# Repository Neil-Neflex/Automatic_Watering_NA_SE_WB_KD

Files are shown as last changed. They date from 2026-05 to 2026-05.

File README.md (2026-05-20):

Ce dépôt est organisé de manière à séparer la documentation de conception du code source technique. Pour naviguer efficacement, le projet utilise deux branches distinctes.

## Organisation des branches

- **Branche main**: Centralise la documentation, les rapports de projet et les études d'impact.
- **Branche partie-logicielle**: Contient exclusivement le code source et les fichiers de configuration.

## Contenu de la branche Main

- **DOCS**: Ressources techniques et rapports des membres du groupe par séance.
- **ecoconception**: Analyse du cycle de vie et choix techniques pour minimiser l'empreinte énergétique.
- **Hardware-pcb-eagle**: Schémas électroniques et fichiers PCB réalisés sous Eagle.
- **ProjetS7.pdf**: Présentation S8.
- **RAPPORT.pdf**: Rapport de synthèse présentant les objectifs et résultats du semestre 7 et 8.

## Architecture logicielle

Le code est segmenté par modules fonctionnels(exemple) :
- **Watering_System.ino**: Point d'entrée principal du programme.
- **SensorManagment (.cpp/.h)**: Logique de traitement des capteurs.
- **VanneCase (.h)**: Gestion des états de l'électrovanne.
- **ModuleHorloge (.cpp/.h)**: Gestion du temps réel (RTC).

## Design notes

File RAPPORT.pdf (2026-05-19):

## Conception d'une station d'arrosage autonome sous ESP32

Projet réalisé dans le cadre de la formation en Ingénierie des Systèmes Embarqués en 4e année
ELSE 4 FISA

### Présenté par :

Ndeye Khady DIOP

Salma ELFIACHE

Wissal BELLAHCEN

### Sous la direction de :

M. Christian PETER

## 1. Introduction générale

## 1.1 Contexte du projet

Dans un contexte mondial marqué par le dérèglement climatique, la gestion raisonnée de l’irrigation représente un enjeu croissant. L’arrosage manuel présente des limites importantes: ils ne tiennent pas compte des conditions météorologiques réelles et conduisent fréquemment à une sur-irrigation néfaste pour l’environnement.
Ce projet s’inscrit dans le cadre du module d'électronique, visant à concevoir un système d’arrosage automatique intelligent, capable de piloter jusqu'à quatres zones d’irrigation de façon indépendante, tout en s’adaptant aux conditions extérieures mesurées en temps réel (température, humidité de l'air, humidité du sol, pluviométrie) .

## 1.2 Problématique

Comment concevoir un système d’arrosage capable de :

- Commander jusqu’à 4 électrovannes de façon indépendante,
- S’adapter en temps réel aux conditions météorologiques (pluie, température, humidité),
- Fonctionner sur batterie avec une autonomie maximale,
- Afficher clairement les informations à l’utilisateur

## 1.3 Objectifs et fonctionnalités attendues

- Pilotage de 4 vannes motorisées 12V (commande impulsionnelle).
- Planification horaire : heure de début et fréquence (en heures) réglables.
- Adaptation automatique : modulation de la durée d’arrosage selon la température et l’humidité de l’air ; annulation en cas de pluie ou de risque de gel.
- Mesure et affichage : température, humidité relative de l'air, humidité du sol (sonde analogique), cumul pluviométrique quotidien, état des vannes.

- Interface utilisateur : écran TFT couleur (ILI9341), avec affichage de logos et de textes.
- Alimentation sur batterie (3,7V Li‑ion) avec convertisseur élévateur 12V pour les vannes.
- Économie d’énergie : utilisation du mode deep sleep et du coprocesseur ULP pour le comptage de la pluie.

## 1.4 Cahier des charges (exigences et contraintes)

## 1.4.1 Description générale

Le système gère 4 circuits d’irrigation indépendants via 4 électrovannes. Les vannes peuvent être activées ou désactivées ; elles sont déclenchées successivement pour éviter une chute de débit. La durée d’arrosage est individuelle par zone, la fréquence est commune. Les mesures des capteurs, la date et l’heure sont affichées en temps réel.

### 1.4.2 Contraintes générales

Domaine | Exigence
Alimentation | Batterie 3,7V + convertisseur 12V pour vannes.
Étanchéité | Boîtier IP65 (extérieur).
Coût | Total <150 € (composants + PCB).
Autonomie | Deep sleep majoritaire, consommation <10 µA en veille.
Reproductibilité | Schéma Eagle, code commenté, BOM fournie.

Simplicité | Pas de dépendance à un serveur distant, paramètres modifiables dans le code.
Interfaces | Compatibilité avec l’ESP32

### 1.4.3 Spécifications fonctionnelles

- Vannes : commande impulsionnelle (5s) non‑bloquante ; pas d’ouverture simultanée.
- Planification : heures de début fixes (ex. 20h00, 20h30…), fréquence en heures (calcul par modulo jours), durée individuelle (minutes).
- Capteurs : DHT22 (température, humidité), pluviomètre à auget (0,2794 mm/basculement), sonde d’humidité du sol (analogique, 0–100%).
- RTC : DS3231 (I2C, pile CR2032 de secours).
- Affichage : écran TFT ILI9341 (SPI), rafraîchissement par flags, logos PNG.
- Adaptation : annulation si pluie >5 mm, T°<4°C, ou sol ≥60% ; modulation durée : +30% si T°≥30°C, –20% si humidité air ≥80%, +20% si sol ≤20%.
- Deep sleep : entrée après 120 secondes d’inactivité (pas d’impulsion pluie, pas d’arrosage). Réveil toutes les 5 minutes. ULP actif pour compter la pluie.

(Les spécifications techniques détaillées des composants sont reportées dans l’état de l’art, section 2.)

## 2. État de l’art et choix technologiques

## 2.1 Choix de l’unité de traitement – ESP32-WROOM-32D

L’ESP32 a été sélectionné pour ses caractéristiques :

- Double cœur Xtensa LX6 à 240 MHz, puissance suffisante pour l’affichage et les algorithmes.
- Coprocesseur ULP (Ultra Low Power) exécutant un programme en assembleur même en deep sleep – indispensable pour compter les impulsions du pluviomètre sans réveiller le CPU.
- Consommation : <10 µA en deep sleep (ULP actif).
- Interfaces : SPI (écran), I2C (RTC), ADC (sol), GPIO (vannes).
- Wi‑Fi/Bluetooth intégrés pour évolutions futures.

Caractéristiques principales : SRAM 520 Ko, Flash 4 Mo, 38 GPIO, ADC 12 bits, alimentation 3,0–3,6 V.

## 2.2 Sélection des capteurs et actionneurs

Type | Modèle | Précision / Sensibilité

Interface

Température /
humidité
DHT22 | ±0,5°C, ±2% HR | 1‑wire (GPIO14,
pull‑up 4,7kΩ)
Pluviomètre | Lexca001 | 0,2794
mm/basculeme
nt

Contact sec,
GPIO34 (pull‑up
externe 10kΩ)

Humidité du
sol

Sonde
capacitive

0–100%
(calibration)

Analogique,
GPIO35

Électrovanne ACARPS IP65
(3 fils)

12V DC, 6W,
commande
impulsionnelle
5s

2 GPIO par
vanne
(ouverture/ferm
eture) via
MOSFET

Détail des vannes : type latching (maintien de position sans courant après impulsion). Pilotage par N‑MOS BSS123 (côté ESP32) et P‑MOS DMP3098 (côté 12V). Résistances de 330 Ω sur les grilles.

## 2.3 Gestion de l’énergie

L’autonomie sur batterie repose sur trois axes complémentaires :

- Architecture d’alimentation : batterie Li-ion 18650 (3,7V, 3000 mAh). Alimentation directe de l’ESP32 (régulateur interne). Un convertisseur élévateur MT3608 fournit le 12V aux vannes. Une diode Schottky SS34 protège contre les inversions de polarité.
- Vannes latching : consommation uniquement pendant l’impulsion de 5 secondes (≈30 J par action), puis zéro.
- Mode deep sleep de l’ESP32 : le CPU est éteint la plupart du temps, seule l’ULP tourne. Consommation <10 µA. L’entrée en veille est conditionnée par l’absence d’arrosage et un délai d’inactivité de 120 secondes. Réveil périodique toutes les 5 minutes.

## 2.4 Interface homme‑machine – Écran TFT ILI9341

Écran 2,4 pouces, 240×320 pixels, 16 bits, piloté en SPI.
Brochage utilisé : MOSI=23, MISO=19, SCK=18, CS=15, DC=5, RST=4, LED=13. Logos PNG (température, humidité, pluie, terre) stockés en mémoire Flash (fichier images.h) et décodés par la bibliothèque PNGdec.

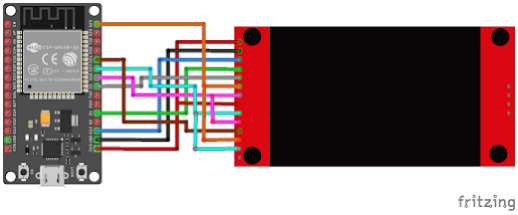
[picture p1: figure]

Shémat de cablage provenant du site : https://electroniqueamateur.blogspot.com/2021/05/utilisation-dun-ecran-ta ctile-tft-spi.html

Voici le branchement de l'écran sur le module ESP32:

- Broche VCC de l'écran: sortie 3,3 V de l'ESP32
- Broche GND de l'écran: broche GND de l'ESP32
- Broche CS de l'écran: broche D15 de l'ESP32
- Broche Reset de l'écran: broche D4 de l'ESP32
- Broche DC de l'écran: broche D5 de l'ESP32
- Broche SDI (MOSI) de l'écran: broche D23 de l'ESP32
- Broche SCK de l'écran: broche D18 de l'ESP32
- Broche LED de l'écran: sortie 3,3 V de l'ESP32
- Broche CDCK (MISO) de l'écran: broche D19 de l'ESP32
- Broche T_CLK de l'écran: broche D18 de l'ESP32
- Broche T_CS de l'écran: broche D21 de l'ESP32
- Broche T_DIN de l'écran: broche D23 de l'ESP32
- Broche T_DO de l'écran: broche D19 de l'ESP32
- Broche T_IRQ de l'écran: pas branchée

## 3. Architecture globale du système

## 3.1 Synoptique matériel

Le système repose sur un ESP32-WROOM assurant l’acquisition des données environnementales, leur traitement et la commande des électrovannes. L’alimentation des actionneurs est assurée par une conversion DC-DC élévatrice, tandis que l’interface utilisateur est réalisée via un écran TFT SPI

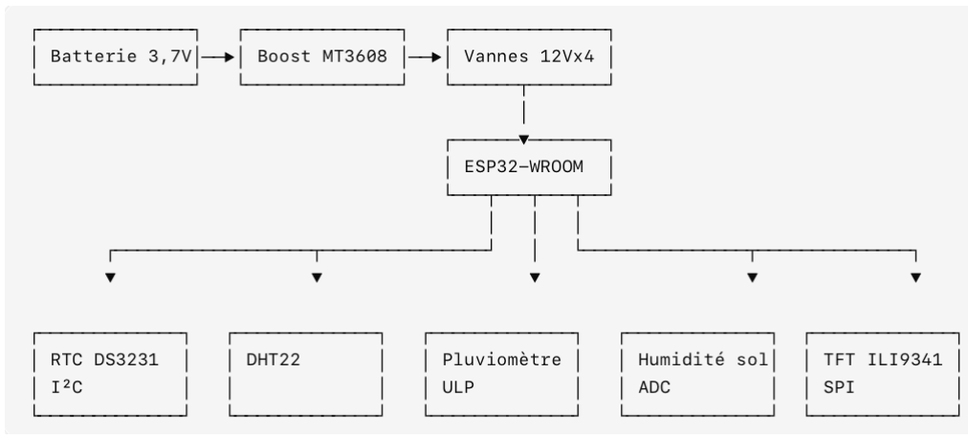
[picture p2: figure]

## 3.2 Modes de fonctionnement

Le système opère selon deux modes distincts, gérés dynamiquement en fonction de l'activité détectée.

Mode actif. À chaque démarrage ou réveil, l'ESP32 initialise l'ensemble des périphériques (RTC DS3231, écran TFT, capteur DHT22) et lance la boucle principale. Celle-ci exécute quatre tâches non-bloquantes par des timers millis() : la mise à jour de l'affichage à la seconde, la lecture des capteurs toutes les 5 secondes, la lecture du compteur pluviométrique toutes les 2 secondes, et la vérification du planning d'arrosage à chaque seconde. L'affichage est actif et l'interface utilisateur réactive aux appuis sur les boutons.

Mode veille profonde (Deep Sleep). Lorsque les conditions du garde-fou sont réunies, l'ESP32 sauvegarde les données persistantes (cumul de pluie, timestamps de fin d'arrosage, horodatage de la dernière pluie) dans la mémoire RTC — la seule zone mémoire qui survit au Deep Sleep — puis entre en sommeil. Un réveil périodique par timer permet de vérifier régulièrement si un arrosage planifié doit être déclenché. Lors du réveil, le système distingue un premier démarrage (remise à zéro de tous les compteurs et initialisation de l'ULP) d'un réveil depuis la veille (restauration des valeurs mémorisées), avant de reprendre la boucle principale.

## 4. Conception logicielle

## 4.1 Architecture Orientée Objet (POO)

Le code est découpé en plusieurs classes pour faciliter la maintenance et l’évolution :

- Case (classe abstraite) : représente une zone rectangulaire de l’écran, avec position, taille, couleur de fond, et un flag de modification.
- SensorCase : hérite de Case, ajoute une valeur entière, une unité, un logo PNG, et la méthode draw() pour afficher ces informations.
- VanneCase : hérite de Case, ajoute un nom, une fréquence (heures), une durée (minutes), l’état (ouverte/fermée) et les GPIO de commande.
- Interface: gère l’écran global, l’affichage de l’heure, et appelle le dessin des cases.
- SensorManagment : regroupe la lecture des capteurs (DHT22, RTC, ULP, sol) et met à jour les objets SensorCase correspondants.

Cette modularité permet d’ajouter facilement un nouveau capteur ou une nouvelle vanne.

## 4.2 Optimisation de l'Interface Homme-Machine

Affichage par flags : chaque case possède un booléen flag qui passe à 1 quand sa valeur ou sa couleur change. La fonction Update() ne redessine que les cases dont le flag est à 1, puis le remet à 0. Cela évite de rafraîchir tout l’écran à chaque seconde et réduit la charge CPU.
Logos PNG : les icônes (température, humidité, pluie, terre) sont stockées en mémoire Flash (via images.h) et décodées avec la bibliothèque PNGdec. Elles sont dessinées une fois lors de l’affichage initial.
Horloge : l’heure est lue depuis le RTC et affichée dans le bandeau supérieur mise à jour chaque seconde.

Couleurs : les arrière‑plans des capteurs changent selon les seuils (rouge = critique, orange/jaune = attention, blanc = normal). Les vannes sont vertes (ouvertes), rouges (désactivées), blanches (fermées).

## 4.3 Logique d'arrosage asynchrone

Algorithme d’arrosage automatique — Description détaillée

### 1. Démarrage du système (phase d’initialisation)

Lorsque l’ESP32 est alimenté ou sort d’une période de veille, le système détermine d’abord la cause du démarrage :
- Premier démarrage (alimentation mise en place):
- Le programme ULP est initialisé dans le coprocesseur basse consommation, chargé de surveiller en permanence le pluviomètre.
- L’ensemble des compteurs est remis à zéro : pluie totale (0 mm), horodatages de fin d’arrosage (0), dernier horodatage de pluie (0).
- Réveil après une période de veille profonde (réveil programmé par temporisateur) :
- Les valeurs conservées avant la mise en veille (pluie totale, horodatage de fin d’arrosage, horodatage de la dernière pluie) sont récupérées depuis la mémoire RTC, qui préserve les données pendant le *deep sleep*.
Dans tous les cas de figure, l’initialisation suivante est effectuée :
- Horloge RTC (module DS3231 via le bus I2C)
- Écran TFT
- Capteur DHT22 (mesure de la température et de l’humidité de l’air)
- Capteur d’humidité du sol (lecture analogique par CAN)
- Affichage principal des valeurs courantes

### 2. Boucle principale

La boucle principale s’exécute en continu et gère cinq tâches concurrentes, non bloquantes, chacune pilotée par des temporisateurs basés sur millis() :

- Tâche A — Mise à jour de l’affichage (périodicité : 1 seconde)
Le gestionnaire d’écran vérifie les zones dont le drapeau de mise à jour est positionné à 1 (valeur modifiée) et ne redessine que ces zones. L’heure est également rafraîchie.
- Tâche B — Lecture des capteurs (périodicité : 5 secondes)
Le capteur DHT22 est interrogé pour obtenir la température (°C) et l’humidité relative de l’air (%). Ces valeurs sont converties en entiers puis stockées dans les zones correspondantes. En cas de changement de valeur, le drapeau de mise à jour est activé, ce qui déclenchera un rafraîchissement de l’affichage au cycle suivant.
- Tâche C — Lecture du pluviomètre (périodicité : 2 secondes) Pendant l’exécution du programme principal, le coprocesseur ULP comptabilise les basculements du pluviomètre. Toutes les 2 secondes, le compteur est lu et remis à zéro. Chaque basculement correspond à une hauteur de pluie de 0,2794 mm.

En cas de nouvelles impulsions détectées :

- La quantité de pluie correspondante est ajoutée au total journalier.
- L’horodatage exact (en secondes Unix, fourni par le RTC) de cette détection est enregistré, afin de déterminer ultérieurement s’« il pleut actuellement » lors de la prise de décision d’arrosage.
- L’affichage de la zone réservée au pluviomètre est mis à jour.
- Tâche D — Lecture de l’humidité du sol (périodicité : 10 secondes) Le capteur d’humidité du sol est lu via le convertisseur analogique-numérique de l’ESP32. La valeur analogique brute est convertie en pourcentage (0 % = sol sec, 100 % = sol saturé). En cas de modification de la valeur, le drapeau de mise à jour est activé, et l’affichage correspondant sera actualisé au cycle suivant.
- Tâche E — Vérification du planning d’arrosage (périodicité : 1 seconde) Cette tâche constitue l’élément central de l’algorithme. Elle est détaillée ci-après.

### 3. Logique de décision d’arrosage (gererVannesAutomatiques)

Cette fonction est appelée chaque seconde, avec l’heure exacte fournie par le RTC. Elle traite indépendamment les quatre vannes, dans l’ordre de la vanne V1 à la vanne V4.
Pour chaque vanne, deux types de vérifications sont effectués :
- Vérification de la condition d’ouverture (déclenchement) Condition de déclenchement horaire :
L’heure courante doit correspondre exactement à l’heure et à la minute programmées pour cette vanne, et la seconde doit être zéro.
Exemple : V1 se déclenche à 20:00:00, V2 à 20:30:00, etc.
Chaque vanne possède une fréquence exprimée en heures (par exemple, 48 h = un arrosage tous les deux jours). Le nombre de jours écoulés depuis le 1ᵉʳ janvier 1970 (timestamp Unix divisé par 86 400) est calculé. Si ce nombre de jours est divisible par l’intervalle programmé, le jour est considéré comme un jour d’arrosage pour cette vanne. Dans le cas contraire, on passe à la vanne suivante.

Si le jour est un jour d’arrosage, les gardes météorologiques sont vérifiées :
- Garde 1 — Pluie accumulée excessive
Si le total des précipitations enregistrées depuis le début de la journée atteint ou dépasse 5 mm, l’arrosage est annulé (le sol a déjà reçu un apport naturel suffisant).
- Garde 2 — Pluie en cours
On détermine si une pluie a été détectée au cours des 15 dernières minutes. Pour cela, l’horodatage RTC actuel est comparé au dernier horodatage enregistré lors d’une détection d’impulsion du pluviomètre. Si la différence est inférieure à 900 secondes (15 min), on considère qu’il pleut encore, et l’arrosage est annulé.
- Garde 3 — Risque de gel
Si la température actuelle est inférieure ou égale à 4 °C, l’arrosage est annulé afin d’éviter le gel de l’eau dans les canalisations et les détériorations associées.
- Garde 4 — Sol déjà suffisamment humide
Si l’humidité mesurée du sol est supérieure ou égale à 60 %, l’arrosage est annulé : le sol contient déjà une quantité d’eau adéquate, et un arrosage supplémentaire serait superflu, voire risquerait d’asphyxier les racines.
Si l’ensemble des gardes est franchi, le système procède au **calcul de la durée d’arrosage** :

La durée de base est celle configurée individuellement pour chaque vanne (en minutes). Cette durée est ensuite modulée par les facteurs suivants :
- Modulateur 1 — Température élevée
- Température ≥ 35 °C : durée × 1,50 (+50 %) — condition caniculaire
- Température comprise entre 30 °C et 35 °C (exclu) : durée × 1,30 (+30 %) — forte chaleur
- Modulateur 2 — Humidité de l’air élevée
- Humidité relative ≥ 80 % : durée × 0,80 (−20 %) — air saturé, évaporation réduite
La durée finale est arrondie à l’entier inférieur, avec un minimum d’une minute.
- Modulateur 3 — Sol très sec
-Humidité du sol ≤ 20 % : durée × 1,20 (+20 %) — sol sec, besoin hydrique accru.
La durée finale est arrondie à l’entier inférieur, avec un minimum d’une minute.
- Déclenchement effectif :
- La vanne est ouverte (envoi d’une impulsion sur la broche GPIO pendant 5 secondes, de manière non bloquante).
- La date et l’heure exactes de fermeture prévue sont calculées : timestamp_fin = timestamp_actuel + (durée_finale × 60 secondes). Cette valeur est conservée en mémoire RTC afin de résister à une éventuelle mise en veille.
- Vérification de la fermeture
À chaque seconde, pour chaque vanne dont l’état est « ouverte » (state = vrai), l’horodatage RTC courant est comparé à l’horodatage de fermeture programmé.
Si l’heure de fin est atteinte ou dépassée, la vanne est fermée (envoi d’une impulsion inverse sur la broche GPIO pendant 5 secondes).

### 4. Remise à zéro quotidienne à minuit

Chaque nuit, à 00:00:00, le système procède une seule fois aux remises à zéro suivantes :
- Total journalier des précipitations
- Horodatage de la dernière pluie détectée
- Affichage associé au pluviomètre

### 5. Gestion des vannes (mode non bloquant)

Les vannes utilisées (modèle ACARPS IP65) sont de type *latching* (motorisées, trois fils) : elles conservent leur position sans consommation de courant une fois actionnées.
Pour les commander, une impulsion de 5 secondes est envoyée sur la broche GPIO correspondante.
Le surveillant `checkTimer()` est appelé à chaque cycle de la boucle principale. Si une impulsion est en cours depuis plus de 5 secondes, il désactive les deux broches GPIO et libère la vanne, sans jamais bloquer le déroulement du programme.

Résumé visuel

CHAQUE SECONDE
│
├── Heure == heure_départ[i] ET seconde == 0 ?
│ └── OUI → Jour d'arrosage (fréquence) ?
│ | └── OUI → GARDE 1 : pluie_totale >= 5mm ? → ANNULER
│ | GARDE 2 : pluie < 15 min ? | → ANNULER
│ | GARDE 3 : temp <= 4°C ? | → ANNULER
│ | GARDE 4 : humidité sol >= 60% ? → ANNULER
│ | └── TOUTES OK → Calculer durée de base
│ | Moduler (temp, humidité air,humidité sol)
│ | Ouvrir vanne
│ | Enregistrer timestamp de fin
│
└── Vanne ouverte ET timestamp_actuel >= timestamp_fin ?
| └── OUI → Fermer vanne

## 4.4 Le coprocesseur ULP

Le coprocesseur ULP (Ultra Low Power) est un processeur auxiliaire intégré à l'ESP32, capable d'exécuter un programme en assembleur pendant que les cœurs principaux sont en Deep Sleep. Sa consommation est de l'ordre de quelques centaines de microampères, ce qui le rend indispensable pour surveiller un signal externe de façon continue sans vider la batterie.

Rôle dans le système:
L'ULP est exclusivement chargé du comptage des impulsions du pluviomètre, connecté sur GPIO34. Le capteur à auget Lexca001 génère un front à chaque basculement, chaque impulsion correspondant à 0,2794 mm de pluie. Surveiller ce signal depuis le cœur principal serait incompatible avec le mode Deep Sleep ; l'ULP prend donc en charge cette tâche de façon transparente.

Configuration de la broche:

Dans la fonction initULP(), GPIO34 est initialisée en entrée RTC via rtc_gpio_init() et rtc_gpio_set_direction(). Les résistances de pull-up et pull-down internes sont explicitement désactivées car une résistance externe de 10 kΩ assure le niveau logique au repos. La fonction rtc_gpio_hold_en() verrouille l'état de la broche pendant le Deep Sleep pour éviter toute dérive.

Programme assembleur ULP:

Le programme est écrit sous forme de tableau d'instructions ulp_insn_t et chargé en mémoire via ulp_process_macros_and_load(). Il s'exécute en boucle toutes les 50 ms (période configurée par ulp_set_wakeup_period(0, 50000)). La logique de détection de front repose sur la comparaison entre l'état courant de la broche et le dernier état mémorisé. Seuls les fronts montants (transition 0→1) incrémentent le compteur, ce qui évite de compter deux fois chaque basculement. Les valeurs sont stockées dans RTC_SLOW_MEM aux adresses 20 (ULP_COUNT_ADDR) et 21 (ULP_LAST_STATE_ADDR), choisies suffisamment hautes pour ne pas entrer en conflit avec le reste du programme et éviter tout crash.

Persistance entre les cycles de veille.

Lors d'un premier démarrage (cause de réveil ≠
ESP_SLEEP_WAKEUP_TIMER), les deux cellules mémoire sont remises à zéro et l'état initial de la broche est supposé à 1 (niveau haut au repos). Lors d'un réveil depuis le Deep Sleep, ces valeurs sont conservées intactes, garantissant qu'aucune impulsion n'est perdue pendant la veille.

Lecture depuis le programme principal. La fonction getPulseCount() lit le compteur via RTC_SLOW_MEM[ULP_COUNT_ADDR] & 0xFFFF, remet immédiatement la case à zéro, et retourne le nombre d'impulsions accumulées depuis la dernière lecture. Ce masque 16 bits évite de lire des bits de statut parasites stockés dans les bits hauts de la mémoire RTC. Cette fonction est appelée toutes les 2 secondes par la tâche C de la boucle principale pour mettre à jour le cumul pluviométrique journalier.

## 4.5 Stratégie énergétique (Deep Sleep)

L'ESP32 est programmé pour entrer en mode Deep Sleep afin de préserver la batterie. Cependant, un algorithme de sécurité a été implémenté pour empêcher une mise en veille critique : le système ne s'endort que si deux conditions strictes sont réunies :

1. Aucune vanne n'est actuellement en cours d'ouverture, pour éviter qu'une vanne ne reste bloquée ouverte pendant le sommeil.
2. Un délai d'inactivité de 120 secondes s'est écoulé sans modification de l'interface (pas de pluie détectée, pas de manipulation).

## 5. Conception matérielle

## 5.1 Saisie du schéma électronique

Le schéma a été réalisé sous Eagle 9.6.2 et il comprend les blocs suivants:

- Alimentation : batterie 3,7V → boost MT3608 → 12V pour vannes. Diode Schottky (D1) pour protection, self 22µH, condensateurs de filtrage.
- ESP32 : module WROOM‑32, avec connecteur pour programmation série (DOWNLOAD : TX, RX, IO0, RST, 3V3, GND).

- Capteurs : DHT22 (pull‑up 4,7kΩ sur GPIO14), pluviomètre sur GPIO34 (pull‑up externe 10kΩ à ajouter), humidité sol sur GPIO35 (à câbler).
- RTC : DS3231, alimenté par la pile CR2032 (VBAT) et par le 3,3V (VCC). I2C avec résistances 4,7kΩ.
- Vannes : 4 canaux, chaque vanne pilotée par deux transistors MOSFET : un BSS123 (N‑MOS) côté ESP32, et un P‑MOS (type DMP3098) côté 12V. Des résistances de limitation (330Ω) sont placées sur les grilles des N‑MOS.
- Écran TFT : connecté en SPI (MOSI, MISO, SCK, CS, DC, RST, LED).
- Connecteurs : BATTERIE (1x5), DOWNLOAD (1x6), JP12 (1x5 pour I2C et 3,3V), VANNE_1..4 (1x3).

## 5.2 Placement et routage (Layout)

Le fichier .brd contient un début de placement et de routage. Les pistes ne sont pas encore finalisées (de nombreuses connexions sont à l’état Unrouted). Les axes d’amélioration sont :

- Terminer le routage avec des largeurs adaptées.
- Ajouter des plans de masse (polygones) pour réduire les interférences.
- Placer les résistances de pull‑up (pluviomètre, I2C) près des broches correspondantes.
- Vérifier l’encombrement pour un boîtier IP65 (dimensions 150×100×50 mm).

## 5.3 État d'avancement matériel

- Prototype sur breadboard : validé pour l’ESP32, le TFT, le DHT22, le RTC . Le pluviomètre a été testé avec une simulation manuelle.
- PCB : non encore fabriqué et les vannes pas encore testées

## 6. Tests et validations

La phase de test a été réalisée sur un prototype fonctionnel assemblé sur breadboard. L'objectif de cette étape était de valider l'acquisition des données, la stabilité de l'architecture logicielle, la gestion énergétique, et de simuler la commande des actionneurs avant l'intégration finale sur le circuit imprimé.

## 6.1 Validation de l'acquisition des données et de l'IHM

- Capteurs environnementaux : La lecture du capteur DHT22 (température et humidité de l'air) et de la sonde analogique (humidité du sol via le convertisseur ADC de l'ESP32) a été validée. Les valeurs remontent correctement et les couleurs de l'interface graphique (IHM) s'adaptent dynamiquement aux seuils critiques (ex: passage au rouge si le sol est très sec).
- Horloge RTC : La communication I2C fonctionne parfaitement. Le module conserve l'heure exacte même lors des redémarrages ou des phases de Deep Sleep grâce à sa pile de sauvegarde.
- Interface graphique : L'optimisation logicielle par flags a prouvé son efficacité. L'écran ne scintille pas, car seules les zones dont les données ont changé sont redessinées, économisant ainsi les ressources du microcontrôleur.

## 6.2 Simulation et validation de la logique des vannes

Bien que les tests de puissance sous 12V et les essais hydrauliques réels des électrovannes n'aient pas encore pu être réalisés, la logique de
commande a été intégralement validée au niveau logiciel :
- Planification et Modulateurs : Le moniteur série a permis de vérifier que l'algorithme calcule correctement les jours d'arrosage. Les modulations de durée et les annulations s'exécutent conformément au cahier des charges.

## 6.3 Validation énergétique (Deep Sleep et ULP)

Le système de gestion de l'énergie a été l'un des points les plus critiques à tester :

- Chronomètre d'inactivité : L'ESP32 bascule avec succès en sommeil profond (Deep Sleep) après 120 secondes d'inactivité, à condition qu'aucune vanne ne soit en cours d'ouverture.
- Comptage ULP : Le coprocesseur ULP reste fonctionnel pendant le sommeil du processeur principal. Les basculements du pluviomètre simulés pendant la veille ont été correctement récupérés et additionnés au réveil du système.

## 7. Conclusion et perspectives

Ce projet a permis de concevoir et de développer un système d’arrosage intelligent basé sur l’ESP32, répondant aux objectifs fixés en début d’étude. L’architecture matérielle et logicielle a été entièrement définie, depuis la conception du schéma électronique jusqu’à la réalisation d’un prototype fonctionnel sur breadboard.

Les principales fonctionnalités attendues ont été validées, notamment la planification automatique de l’arrosage, l’adaptation du fonctionnement en fonction des conditions météorologiques (température, humidité de l'air et du sol), ainsi que la commande impulsionnelle et non-bloquante de plusieurs électrovannes. L’intégration du coprocesseur ULP en langage assembleur pour le comptage pluviométrique, couplée à la mise en œuvre effective du mode deep sleep, constitue un apport technique majeur. Cela permet d’optimiser drastiquement la consommation énergétique tout en assurant une surveillance continue. Par ailleurs, l’architecture logicielle orientée objet mise en place facilite grandement la maintenance, la lisibilité du code et l’ajout futur de nouvelles fonctionnalités. Les différentes contraintes rencontrées au cours du développement, telles que la gestion de la mémoire partagée de l'ULP, la création d'un chronomètre d'inactivité ou les conflits matériels des broches, ont également été identifiées puis rigoureusement corrigées.

Certaines étapes restent toutefois à finaliser pour aboutir à un produit totalement abouti. La finalisation du routage et la fabrication d’un circuit imprimé constitueront une étape essentielle vers une version plus robuste et industrialisable du prototype, permettant de tester le pilotage de puissance réel des vannes sous 12V. En l'état, il constitue d'ores et déjà une solution complète, autonome et fonctionnelle, prête à affronter les conditions réelles d'utilisation.

## Annexes

Annexe A – Schéma électrique

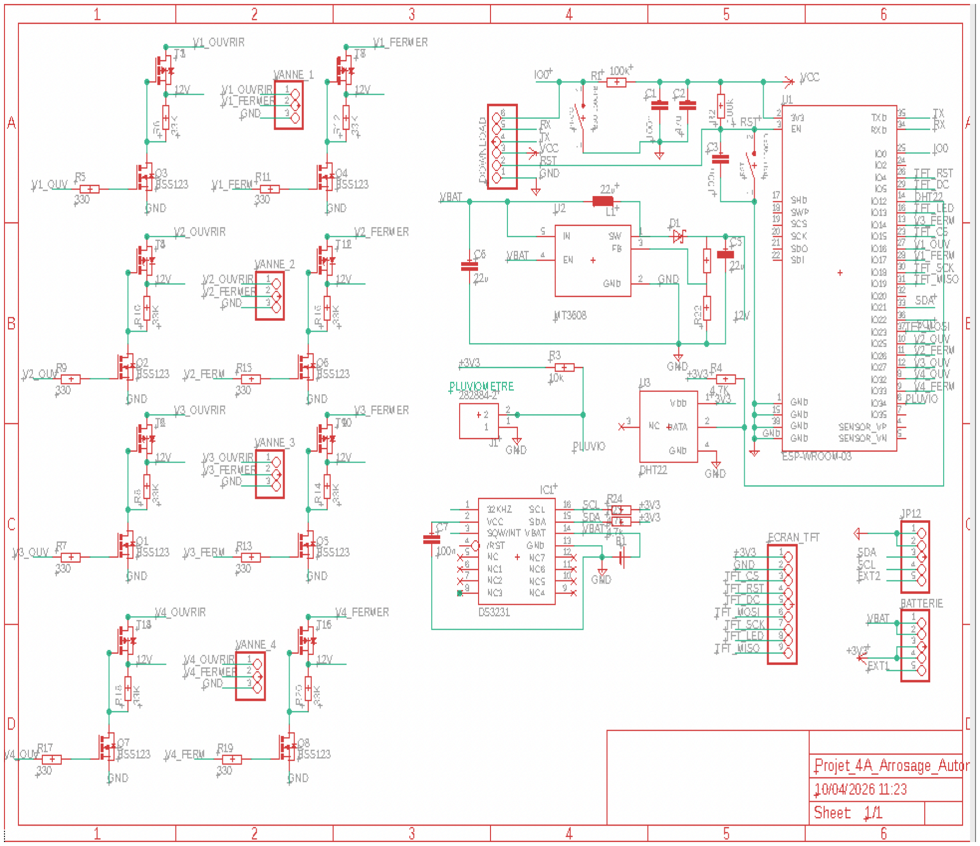
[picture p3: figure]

Annexe B – Code source complet
Dépôt Git contenant les fichiers .ino, .h, .cpp

Annexe C – Liste des bibliothèques utilisées

Bibliothèque | Version | Utilisation
TFT_eSPI | 2.5.0 | Pilotage écran ILI9341
PNGdec | 1.1.1 | Décodage PNG (logos)
RTClib | 2.1.0 | Gestion RTC DS3231
DHT sensor library | 1.4.4 | Lecture DHT22
Adafruit_Sensor | 1.1.6 | Interface capteurs (dépendance)
Wire, SPI, esp32/ulp.h, driver/rtc_io.h | (core ESP32) | I2C, SPI, ULP, deep sleep

Annexe D – Liste du matériel

Référence | Désignation | Qté
ESP-WROOM-32 | Module ESP32 | 1
MT3608 | Boost 12V | 1
DS3231 | Module RTC avec pile | 1
DHT22 | Capteur T/H | 1
Pluviomètre | Lexca001 (auget) | 1
Vanne ACARPS | 12V 3 fils | 4
BSS123 | N‑MOS SOT23 | 8
DMP3098 (ou équivalent) | P‑MOS SOT23 | 8
Résistances 330Ω, 10kΩ, 4,7kΩ | divers | 20
Condensateurs 22µF, 100nF | 0805 | 6
Self 22µH | 0805 | 1
Diode Schottky SS34 | DO‑214 | 1
Écran TFT ILI9341 | SPI 2,4" | 1
Connecteurs 1x3, 1x5, 1x6 | pitch 2,54 mm | 6
Batterie 18650 | 3,7V | 1
Boîtier IP65 | 150×100×50 mm | 1

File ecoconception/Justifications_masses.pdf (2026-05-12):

## 1 Calculs de masse détaillés

Note méthodologique générale : les masses unitaires proviennent de fiches techniques constructeurs ou de bases de données distributeurs (Mouser, LCSC, TME). Pour les composants sans donnée directe, une masse moyenne est estimée sur la base de composants de boîtier et technologie équivalents .

### 1.1 Résistances (24 pièces, boîtier 0805)

Masse unitaire = 0,03 g. Masse totale = 24 × 0,03 = 0,72 g
Source : la masse des résistances CMS 0805 est typiquement comprise entre 0,02 g et 0,03 g (observations sur références courantes). La valeur 0,03 g est retenue comme valeur haute réaliste.

### 1.2 Condensateurs (6 pièces)

Type | Valeur Boîtier Quantité Masse totale (g)
Céramique | 100 nF | 0805 | 3 | 0,09
Électrolytique 10 µF | 1206 | 1 | 0,10
Céramique | 22 µF | 1206 | 2 | 0,20

Masse totale condensateurs = 0,39 g
Sources : condensateur céramique 0805 : masse typique 5,5 mg (Kemet série C0805) ; condensateur 1206 : environ 0,03 g (valeur brute). Les valeurs retenues (0,03 g pour 0805, 0,10 g pour 1206) sont des arrondis incluant l’emballage.

### 1.3 Transistors MOSFET (16 pièces, boîtier SOT-23)

— BSS123 (N-MOSFET) : 8 pièces × 0,035 g = 0,28 g
— AO3401 (P-MOSFET) : 8 pièces × 0,035 g = 0,28 g
Masse totale = 0,56 g
Sources : d’après fiches techniques, BSS123 en SOT-23 pèse entre 0,030 g et 0,036 g ; AO3401 entre 0,031 g et 0,039 g. La moyenne 0,035 g est adoptée pour uniformiser.

### 1.4 Circuits intégrés (5 pièces)

Composant | Référence | Masse unitaire (g) Masse totale (g)
Module ESP32 | ESP-WROOM-32 3,00 | 3,00
Convertisseur boost | MT3608 | 0,05 | 0,05
RTC | DS3231 | 0,50 | 0,50
Capteur T/H | DHT22 | 2,40 | 2,40
Pluviomètre (modélisé) (générique) | 0,10 | 0,10

Masse totale circuits intégrés = 6,05 g
Sources :

— ESP32 : Mouser / Espressif indique 2,5 g ; LCSC 3 g – valeur retenue 3,00 g.
— MT3608 : JLCSMT mentionne 0,00005 kg soit 0,05 g.
— DS3231 : LCSC (0,514 g), TME (0,48 g) – moyenne 0,50 g.
— DHT22 : le marché donne des valeurs très variables (2,4 g à 5,9 g). La valeur 2,40 g est retenue.
— Pluviomètre : estimation basée sur la catégorie « integrated circuit, logic type » (masse générique 0,10 g).

### 1.5 Diode (1 pièce SS34, boîtier SMA)

Masse unitaire = 0,064 g → 0,064 g
Source : caractéristiques techniques de la diode SS34 en boîtier SMA (masse 0,064 g).

### 1.6 Inductance (1 pièce 22 µH)

Masse unitaire = 0,10 g → 0,10 g
Source : inductance SMD standard 22 µH – masse comprise entre 0,05 g et 0,10 g selon les modèles. Valeur maximale retenue.

### 1.7 Support de pile CR2032

Masse unitaire = 1,00 g → 1,00 g Source : estimation

### 1.8 Connecteurs (9 pièces)

Type | Quantité Masse unitaire (g) Masse totale (g)
Bornier 3 broches (vanne) | 4 | 1,00 | 4,00
Bornier 2 broches (pluviomètre) | 1 | 0,80 | 0,80
Header 8 broches (écran) | 1 | 1,00 | 1,00
Header 6 broches (FTDI) | 1 | 0,80 | 0,80
Header 5 broches (batterie) | 1 | 0,70 | 0,70
Header 5 broches (I2C) | 1 | 0,70 | 0,70

Masse totale = 8,00 g

### 1.9 PCB

Masse totale estimée = 50,00 g
Justification : Un PCB FR4 1,6 mm d’épaisseur a une densité surfacique d’environ 3,5 kg/m². Pour 100 cm² (0,01 m²) : 3,5 × 0,01 = 0,035 kg = 35 g (simple face). Avec les couches de cuivre, trous métallisés et masque, la masse réelle se situe entre 50 g et 60 g. La valeur 50 g est retenue.

### 1.10 Actionneurs – 4 électrovannes ACARPS 12V

Masse unitaire estimée par vanne = 300 g. Masse totale pour 4 vannes = 1200 g, décomposée ainsi :
— Laiton (corps) : 960 g (80 %)
— Moteur électrique + engrenages : 240 g (20 %)
Source : les électrovannes motorisées 12V de type ACARPS (corps laiton) ont une masse comprise entre 300 g et 500 g.

### 1.11 Plastiques divers (boîtiers des vannes, support pile, pile CR2032)

Masse totale = 244,60 g, dont :
— Boîtier plastique des 4 vannes : 240 g
— Support pile CR2032 : 1 g
— Pile bouton CR2032 (3 V, non rechargeable) : 3 g

### 1.12 Batterie principale Li-ion

Type : battery, Li-ion, NMC111, rechargeable : masse modélisée : 45 g Justification : Une batterie Li-ion NMC111 de 12 V a typiquement une masse de 0,5 kg pour 7 Ah. Le choix 45 g correspond à une batterie de très faible capacité (1,3 Ah), adaptée à une recharge quotidienne.

### 1.13 Récapitulatif des masses

Masse (g)

Résistances | 0,72
Condensateurs | 0,39
Transistors | 0,56
Circuits intégrés | 6,05
Diode | 0,064
Inductance | 0,10
Support pile | (inclus dans plastiques)
Connecteurs | 8,00
PCB | 50,00
Laiton (vannes) | 960,00
Moteurs (vannes) | 240,00
Plastiques divers (boîtiers + support + pile CR2032) | 244,60
Batterie Li-ion | 45,00
TOTAL | 1555,58

## 2 Calcul de la consommation électrique (90 jours)

Les électrovannes sont au nombre de 4, chacune d’une puissance de 6 W. Elles sont activées 15 minutes par vanne chaque jour, soit un temps total d’activation par jour de :

4 × 15 min = 60 min = 1 heure.

Puissance totale des 4 vannes :

Pvannes = 4 × 6 = 24 W.

Énergie électrique brute (nécessaire aux vannes) par jour :

Ebrute, jour = 24 W × 1 h = 24 Wh.

Sur 90 jours :

Ebrute, 90j = 24 × 90 = 2160 Wh = 2, 160 kWh.

Le convertisseur boost MT3608 a un rendement de 80 %, donc l’énergie prélevée sur la batterie est :

Evannes, batterie =

2, 160
0, 80

= 2, 700 kWh.

La carte électronique (ESP32, capteurs) consomme 0,9 Wh sur 90 jours, soit :

Ecarte = 0, 0009 kWh.

Énergie totale stockée dans la batterie :

Estock = 2, 700 + 0, 0009 = 2, 7009 kWh.

Le chargeur de batterie a un rendement de 85 %. L’énergie prélevée sur le secteur est donc :

Esecteur =

2, 7009
0, 85

≈ 3, 17753 kWh.

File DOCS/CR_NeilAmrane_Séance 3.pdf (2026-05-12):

### Neil AMRANE - ELSE 4 FISA - ANNÉE 2025-2026

# Compte rendu Séance 3

## SYSTÈME D’ARROSAGE AUTOMATIQUE GÉRÉ PAR ESP32

# Introduction

Le projet “Arrosage Automatique contrôlé par ESP32” est un projet tutoré par Christian Peter dans le cadre du projet d’électronique S7 ELSE 4 FISA. Ce projet est mené en collaboration par Neil Amrane, Salma Elfiache, Wissal Bellahcen et Khady Ndyé Diop.

Cet enseignement a pour but de développer un esprit de collaboration et une dynamique créative tout en favorisant l’autonomie dans la création d’un dispositif fonctionnel. Ce projet permet, en outre, de se familiariser avec l’électronique haut niveau et l’interconnection de différents sous-systèmes électroniques en observant un projet dans sa globalité avec ses tenants et aboutissants.

L’objectif est de créer un système d’arrosage automatique permettant de contrôler 4 voies individuellement en programmant la durée d’arrosage de chaque voie et la fréquence d’arrosage des 4 voies. Ce même système intègre différents capteurs qui permettent de mieux gérer l’irrigation des zones couvertes par les circuits d’arrosage et de préserver la biodiversité en tenant compte des données géologiques et atmosphériques réelles et locales

# Compte-rendu

Faire CR Projet S7 : aide aux différents membres du groupe sur programmation et compréhension des procédés; test des électrovanne sur banc de test avec alim DC : Pb de connection pinces crocos...; reflexion autour du shéma électronique avec prof ... Assez d'IO ? ; bilan de composants; début programmation écran LED.

1- Débriefing avec l’équipe des différentes avancées.

A ce stade du projet, les idées générales ont été posées et le cahier des charges a été validé par les membres du groupe. Pour l’instant quelques bouts de codes ont vu le jour mais aucun rendu concret.

Une partie de ma séance a été dédiée à aider les membres du groupe sur certaines erreurs de programmation, ainsi qu’à expliquer le processus et la logique de fonctionnement du système.

Cette étape est cruciale pour développer une dynamique de groupe efficace et ne pas perdre du temps sur la suite du projet.

### 2- Test des électrovannes

Nous avons poursuivi notre séance (avec Khadi) en testant les électrovannes sans pression afin de vérifier leur fonctionnement pratique.

Nous avons utilisé une alimentation DC paramétrée en 12V et nous avons alimenté l’électrovanne à l’aide de pince ‘croco’ et de câbles “Banane-Banane”

Nous avons rencontré des difficultés à alimenter l’électrovanne, du fait des connexions certainement usées par le temps. (recouper les câbles et installer des connecteurs sera probablement utile)

Le test a montré que l’électrovanne tirait ~120mA à l’ouverture et à la fermeture.

Cette valeur est inférieur à la valeur théorique qui était de 500mA à partir de la datasheet constructeur qui annonçait 12V DC 6W (soit 500mA de consommation)

On suppose que l’électrovanne atteint la consommation de 500 mA lorsque le circuit d’eau est sous pression.

Dans le cadre de ce projet, la contrainte de pression n’est pas incluse. En pratique, les différents niveaux (hauteurs des planchers à irriguer) imposant une pression suffisante pour acheminer l’eau jusqu’au niveau souhaité, nous obligerait à calculer (ou vérifier expérimentalement) la consommation en courant pour l’ouverture de l’électrovanne à la pression nécessaire au fonctionnement de l’installation prévue au cahier des charges.

### 3- Réflexion autour du schéma électronique

J’ai ensuite continué en travaillant avec notre professeur, M. Peter, sur le schéma électronique à transistors MOSFET. Nous avons choisi un montage à deux transistors à effet de champ, afin d’activer un transistor acceptant 12V 1A à partir d’un signal de 3,3V. Ce travail a été l’occasion de réactiver certaines notions autour des transistors.

Le premier MOSFET canal-N est activé par une tension VGS de 3,3V, le Drain de ce premier transistor est connecté à la grille du MOSFET canal-P qui est passant lorsque sa grille est à la masse.

### 4- Bilan GPIO

Le travail précédent a aussi mis en lumière le fait qu’avec cette approche, 8 GPIO étaient nécessaires pour actionner nos électrovannes. Nous avons donc, avec Wissal, réalisé le bilan des broches nécessaires à notre projet, afin de savoir si nous pouvions conserver ce montage ou si nous devions adopter une approche moins coûteuse en GPIO.

Ce bilan GPIO a montré que nous avions suffisamment d’IO sur le module ESP32 dont nous disposons pour poursuivre avec ce schéma.

Nous devons maintenant déterminer la référence des deux transistors à utiliser.

### 5- Début du codage de l’écran LED

J’ai entrepris de commencer la programmation de l’Interface Homme-Machine (IHM) afin de pouvoir intégrer les différentes informations au fur et à mesure.

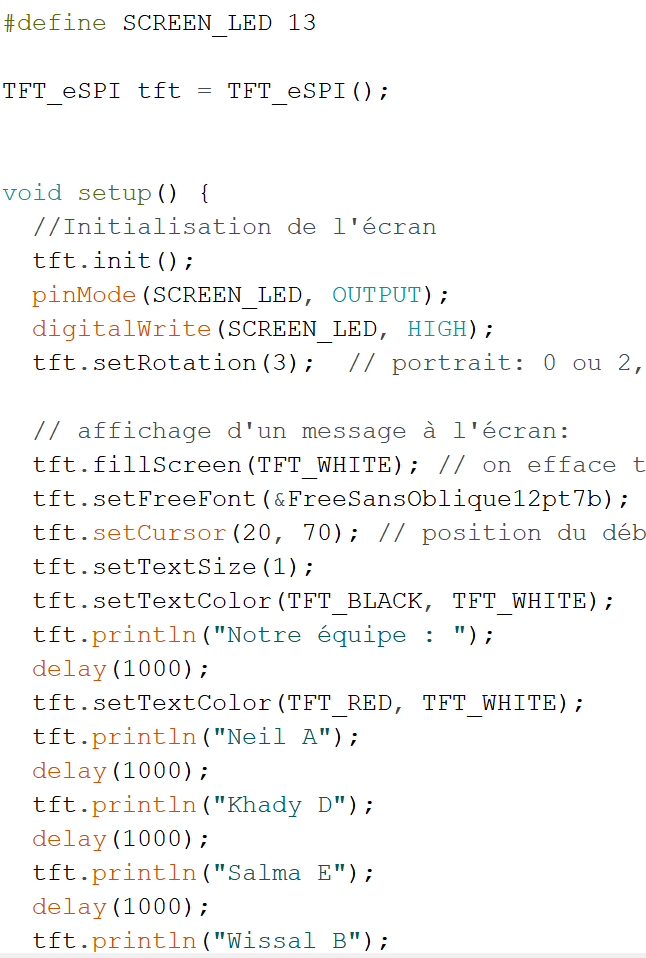
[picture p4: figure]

FIN DE COMPTE RENDU – RÉALISÉ LE 9/11/2025 – NEIL AMRANE

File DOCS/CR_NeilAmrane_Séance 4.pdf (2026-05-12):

### Neil AMRANE - ELSE 4 FISA - ANNÉE 2025-2026

# Compte rendu Séance 4

## SYSTÈME D’ARROSAGE AUTOMATIQUE GÉRÉ PAR ESP32

# Introduction

Le projet “Arrosage Automatique contrôlé par ESP32” est un projet tutoré par Christian Peter dans le cadre du projet d’électronique S7 ELSE 4 FISA. Ce projet est mené en collaboration par Neil Amrane, Salma Elfiache, Wissal Bellahcen et Khady Ndyé Diop.

Cet enseignement a pour but de développer un esprit de collaboration et une dynamique créative tout en favorisant l’autonomie dans la création d’un dispositif fonctionnel. Ce projet permet, en outre, de se familiariser avec l’électronique haut niveau et l’interconnection de différents sous-systèmes électroniques en observant un projet dans sa globalité avec ses tenants et aboutissants.

L’objectif est de créer un système d’arrosage automatique permettant de contrôler 4 voies individuellement en programmant la durée d’arrosage de chaque voie et la fréquence d’arrosage des 4 voies. Ce même système intègre différents capteurs qui permettent de mieux gérer l’irrigation des zones couvertes par les circuits d’arrosage et de préserver la biodiversité en tenant compte des données géologiques et atmosphériques réelles et locales

# Séance 4 - Schéma électronique

Cette séance a été consacrée principalement à la réalisation du schéma électronique du système et à la réalisation de la liste exhaustive des composants du système.

A la séance 3, il a été établi que nous avions assez de GPIO pour valider le montage utilisant 2 GPIO, 2 MOSFET canal-P et 2 MOSFET canal-N par électrovanne.

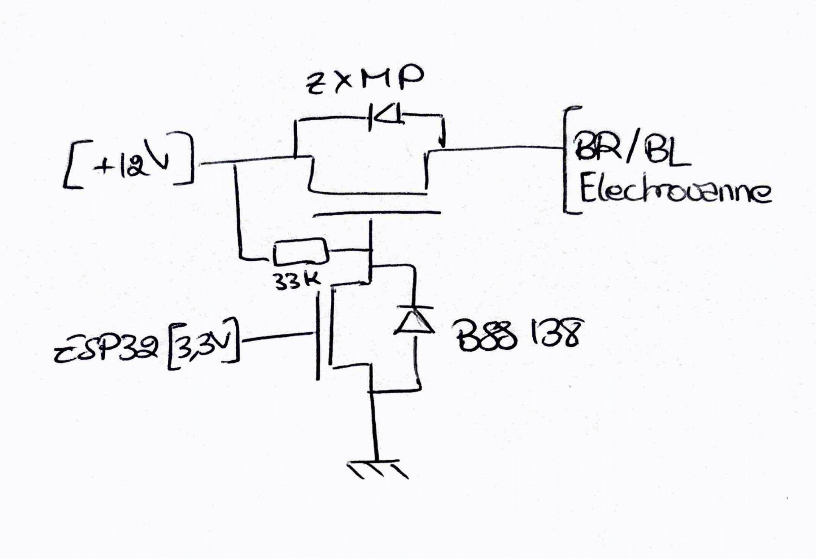
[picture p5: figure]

Pour le canal N, le BSS138 a été choisi et pour le canal P, le ZXMP6A13FTA.

On ajoute une résistance de 33K pour assurer que le ZXMP est bien bloqué tant qu’une tension de 3,3V n’est pas appliquée sur la grille du BSS138.

Pour trouver la référence du ZXMP, M. Peter m’a conseillé le site RS Composant (https://www.lcsc.com/search?q=ZXMP6A13FTA&s_z=n_ZXMP6A13FTA) pour choisir le MOSFET en fonction des caractéristiques Vds, Vgs, Ids et le site LCSC Electronics (https://befr.rs-online.com/web/c/semiconductors/discrete-semiconductors/mosfets/) pour vérifier que la référence existe chez les fournisseurs.

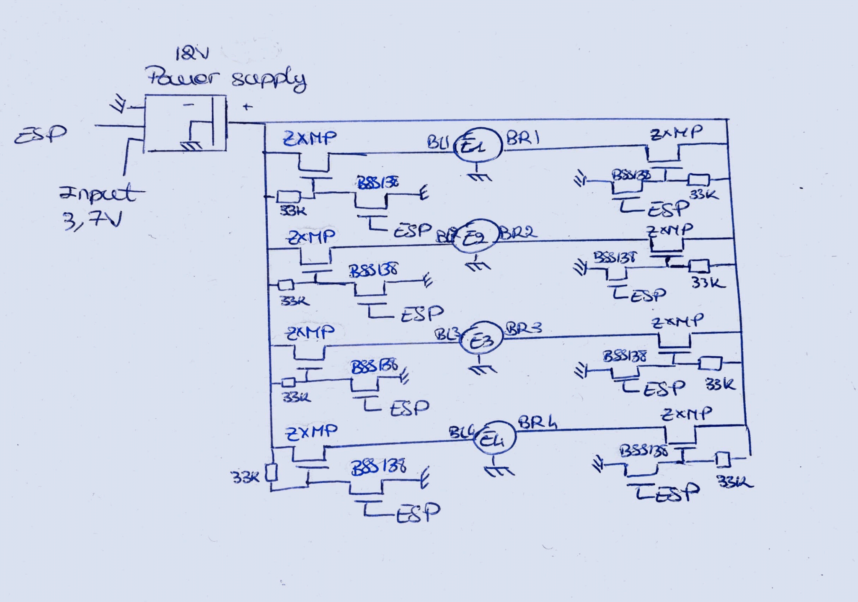
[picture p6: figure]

E1,E2,E3,E4 les 4 électrovannes que contrôle le système. Power supply, le réhausseur de tension MT3608

Le MT3608 est un module qui convertit le 3,7V

La tension de retour doit être de 0,6V en entrée FB. Notre tension cible est 12V.

Vin
Vs⋅ =

R1
(R1+R2) ⇔

Vin
Vs⋅

### - (R1 + R2) = R1 ⇔ R2 = 19 · R1

On récupère la valeur de courant type en sortie de FB = -10nA. On en déduit alors la résistance R1

### Vr1 = IFB · R1 ⇔ 0, 6 V = 10 · E

−9
- R1

Finalement on souhaite que R1 + R2 soit inférieur à 1MOhm soit R1 < 50KOhm

On décide de respecter la série E12 de résistance.

On trouve donc R1 = 10kOhm et R2 = 190KOhm

J’ai ensuite établi la liste des composants nécessaires pour notre système :

Composant | Quantité
Ecran LED | 1
ESP32 WROM 32D | 1
Batterie 3,7V 20000mAh | 1
Electrovanne 3 fils | 4
Pluviomètre | 1
DHT22 | 1
Module horloge | 1
Module réhausseur de tension MT3608 | 1
MOSFET BSS138 | 8
MOSFET ZXMP6A13FTA | 8
Résistance SE12 4,7KOhm | 1
Résistance SE12 190KOhm | 1
Résistance SE12 10KOhm | 2
Résistance SE12 33KOhm | 8
Câbles dupont Mâle-Femelle | Qtt suffisantes
Bouton pression | 4

Pour la réalisation du boitier :
Composant | Quantité
Boitier Electrique PVC dim suffisantes | 1
Morceau de Plexi ou PVC transparent 2mm 10x10cm | 1
Connecteurs étanches 4mm section | 4
Colle chaude | Qtt suffisantes

Gaine Thermo rétractable | Qtt suffisantes
Entretoises et visserie | Qtt suffisantes
Connecteur d’alimentation étanche | 1
Bouton d’alimentation étanche | 1

Pour la prochaine séance, je me concentrerai sur l’IHM en programmant la partie écran du système.

FIN DE COMPTE RENDU – FAIT À NICE – LE 15/11/2025

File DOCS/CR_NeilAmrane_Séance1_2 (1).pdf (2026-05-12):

### Neil AMRANE - ELSE 4 FISA - ANNÉE 2025-2026

# Compte rendu Séance 1 & Séance 2

## SYSTÈME D’ARROSAGE AUTOMATIQUE GÉRÉ PAR ESP32

# Introduction

Le projet “Arrosage Automatique contrôlé par ESP32” est un projet tutoré par Christian Peter dans le cadre du projet d’électronique S7 ELSE 4 FISA. Ce projet est mené en collaboration par Neil Amrane, Salma Elfiache, Wissal Bellahcen et Khady Ndyé Diop.

Cet enseignement a pour but de développer un esprit de collaboration et une dynamique créative tout en favorisant l’autonomie dans la création d’un dispositif fonctionnel. Ce projet permet, en outre, de se familiariser avec l’électronique haut niveau et l’interconnection de différents sous-systèmes électroniques en observant un projet dans sa globalité avec ses tenants et aboutissants.

L’objectif est de créer un système d’arrosage automatique permettant de contrôler 4 voies individuellement en programmant la durée d’arrosage de chaque voie et la fréquence d’arrosage des 4 voies. Ce même système intègre différents capteurs qui permettent de mieux gérer l’irrigation des zones couvertes par les circuits d’arrosage et de préserver la biodiversité en tenant compte des données géologiques et atmosphériques réelles et locales

# Séance 1 - Initialisation du projet

La première séance a été dédiée à la définition et au dimensionnement du projet. J’ai défini le plan du Cahier des charges que nous avons ajusté et validé de façon collégiale. J’ai ensuite pris en charge la description générale du processus. J’ai ensuite débuté la réalisation du visuel de l’IHM (Interface Homme Machine).

## Sommaire du Cahier des Charges

1. Introduction (https://docs.google.com/document/d/1gFn5o0FpMJYlvrdDOcBcZvFx4WQceKKxzy86QO6qI9Y/edit?tab=t.0)
2. Description générale du processus (https://docs.google.com/document/d/1gFn5o0FpMJYlvrdDOcBcZvFx4WQceKKxzy86QO6qI9Y/edit?tab=t.0)
3. Contraintes (https://docs.google.com/document/d/1gFn5o0FpMJYlvrdDOcBcZvFx4WQceKKxzy86QO6qI9Y/edit?tab=t.0)
a. fonctionnelles
b. techniques
4. Spécifications composants matériel (https://docs.google.com/document/d/1gFn5o0FpMJYlvrdDOcBcZvFx4WQceKKxzy86QO6qI9Y/edit?tab=t.0)
a. ESP32 (https://docs.google.com/document/d/1gFn5o0FpMJYlvrdDOcBcZvFx4WQceKKxzy86QO6qI9Y/edit?tab=t.0)
b. Module Horloge
c. DHT11 (Hygrométrie et Température) (https://docs.google.com/document/d/1gFn5o0FpMJYlvrdDOcBcZvFx4WQceKKxzy86QO6qI9Y/edit?tab=t.0)
d. Pluviomètre (https://docs.google.com/document/d/1gFn5o0FpMJYlvrdDOcBcZvFx4WQceKKxzy86QO6qI9Y/edit?tab=t.0)
e. Electrovannes ACARPS IP65 [3 wires 2 control] (https://docs.google.com/document/d/1gFn5o0FpMJYlvrdDOcBcZvFx4WQceKKxzy86QO6qI9Y/edit?tab=t.0)

5. Gestion Power Supply (https://docs.google.com/document/d/1gFn5o0FpMJYlvrdDOcBcZvFx4WQceKKxzy86QO6qI9Y/edit?tab=t.0)
6. Dispositif d’affichage HMI (https://docs.google.com/document/d/1gFn5o0FpMJYlvrdDOcBcZvFx4WQceKKxzy86QO6qI9Y/edit?tab=t.0)

## Description générale du processus

Le système d’arrosage automatique est en mesure de gérer 4 circuits d’irrigation indépendants à partir d’une arrivée d’eau via 4 électrovannes indépendantes. Il dispose d’un petit écran LED ainsi que 4 boutons cliquables qui constituent l’interface homme-machine (HMI). Le dispositif est contrôlé par un module ESP32 WIFI programmé en C++, intégré au circuit imprimé. On retrouve également un capteur d'hygrométrie, de température et de pluviométrie.

Les différentes pistes (vannes) peuvent être activées ou désactivées. Lorsqu’elles sont activées, les pistes sont déclenchées successivement. La fréquence d’arrosage est commune aux 4 pistes, pour éviter l’ouverture de deux vannes en même temps (ce qui entraînerait la réduction du débit dans les circuits d’eau).
La durée d’arrosage (durée pendant laquelle la vanne est ouverte) est individuelle pour chaque piste, de façon à adapter l’irrigation au besoin des différentes zones.

Les différentes mesures prises par les capteurs ainsi que la date et l’heure sont affichées sur l’écran du système. Ces mesures sont utilisées par le dispositif pour adapter l’arrosage aux conditions extérieures réelles, et ainsi éviter la sur-irrigation en période pluvieuse ou à l’inverse le manque d’irrigation en période de sécheresse.

Dans un second temps, la connectivité WIFI du module ESP32 permettra le transfert des données sur un serveur distant et le contrôle du dispositif via une application mobile.

# Séance 2 - Organisation générale et précision des composants

Le début de cette deuxième séance a été dédié à la validation des parties du cahier des charges déjà rédigées et à la poursuite du cahier des charges.

J’ai ensuite mis en place un outil de gestions des tâches partagées sur google sheet (je suis conscient qu’un tableau de bord existe sur gitHub, mais je suis plus à l’aise sur Sheet) et j’ai défini les missions initiales inhérentes au projet.

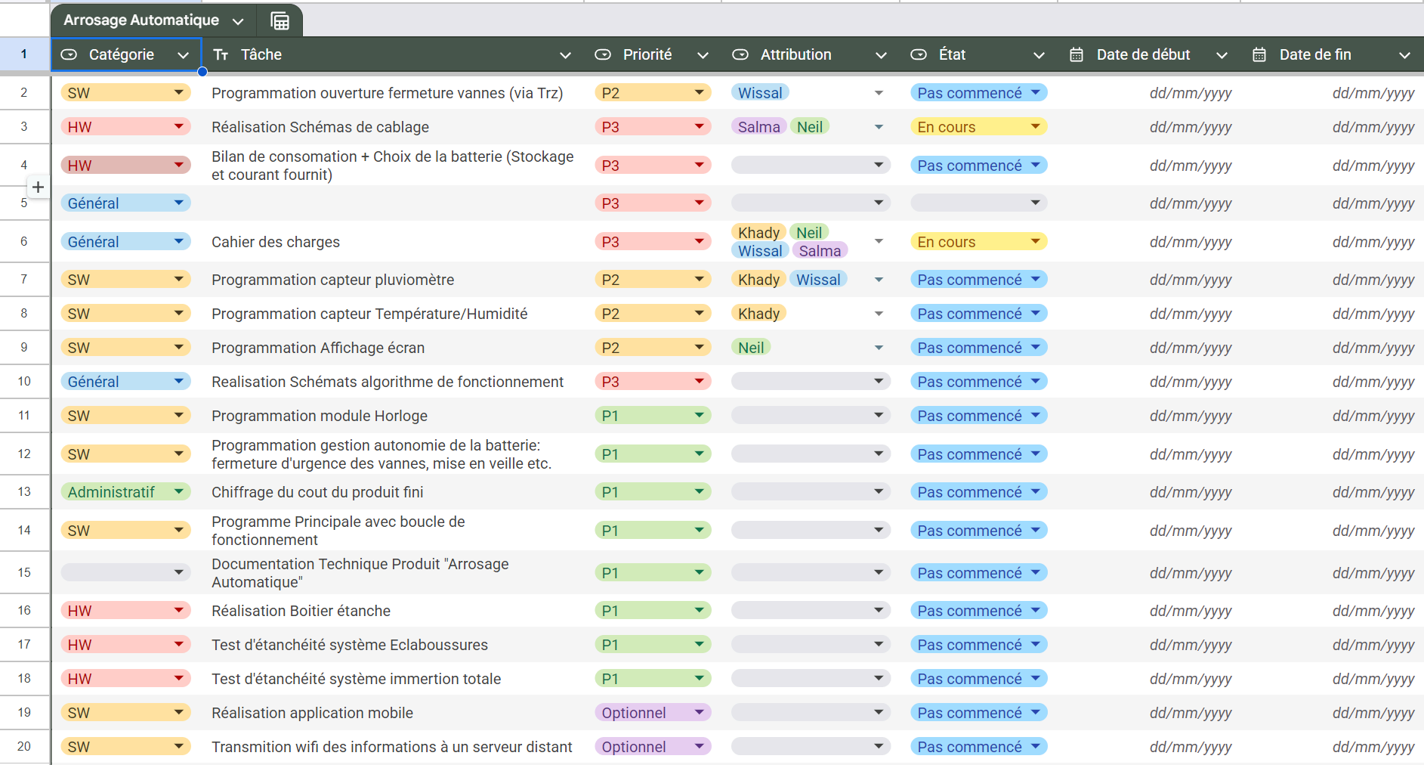
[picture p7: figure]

J’ai ensuite achevé et fait valider par le reste de l’équipe, le visuel de l’interface graphique de l’IHM de l’arrosage automatique. J’ai défini plusieurs exemples représentant les différentes fonctionnalités du système d’arrosage automatique.

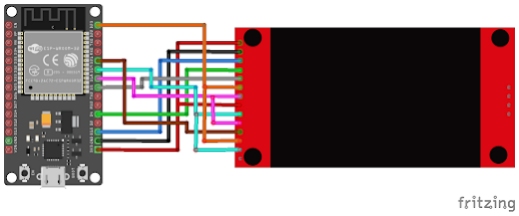
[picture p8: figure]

schéma de câblage de l’écran LED utilisé pour l’IHM

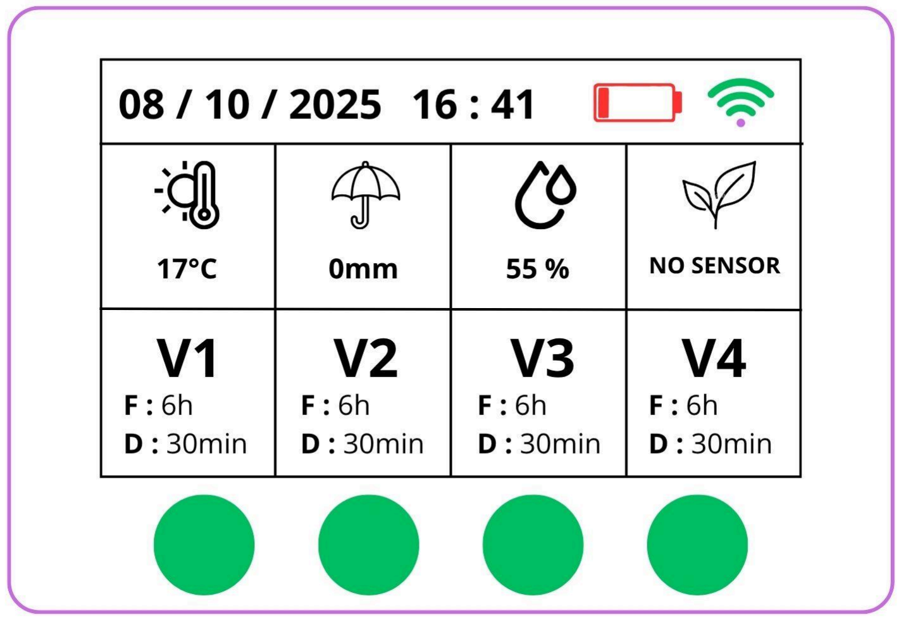
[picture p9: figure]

Interface standard de l’HMI

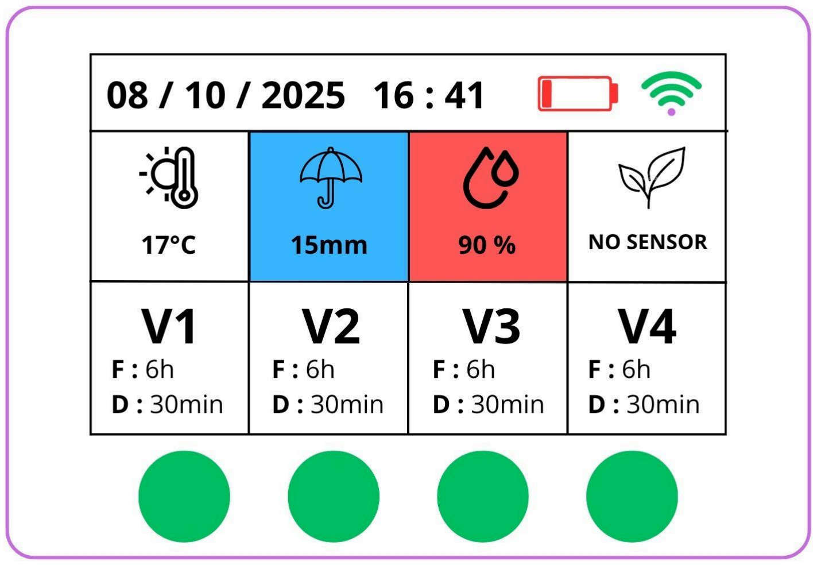
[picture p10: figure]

Interface de l’HMI où l’affichage indique une pluie importante

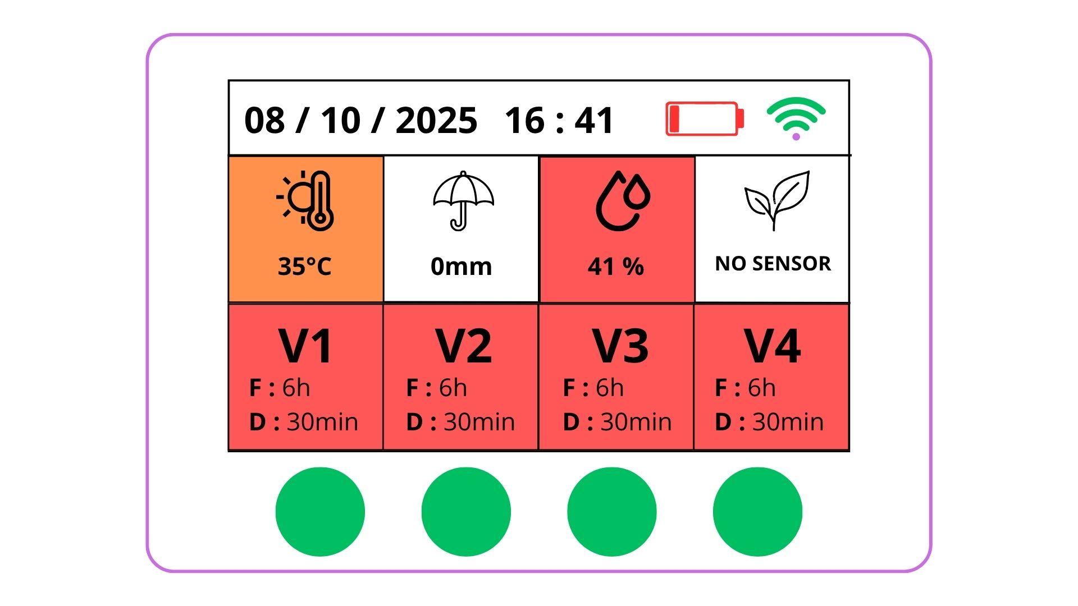
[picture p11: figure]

Interface de l’HMI où l’affichage indique une température trop élevée pour arroser, les vannes sont alors verrouillées tant que la température n’est pas redescendue. (option pouvant être désactivée)

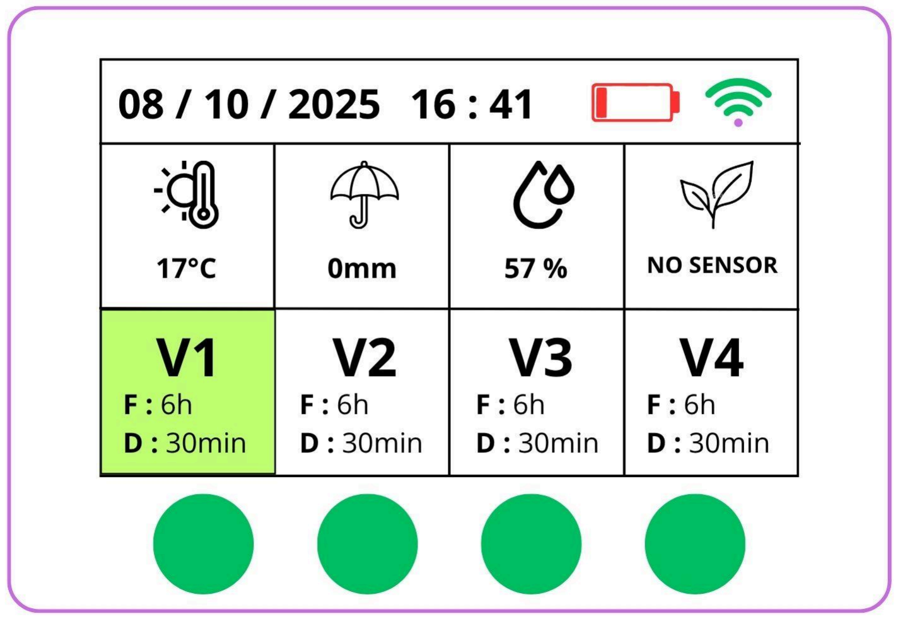
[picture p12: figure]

Interface de l’HMI affichant l’état ouvert de l’une des électrovannes

J’ai ensuite commencé à travailler sur le câblage et le contrôle des électrovannes via deux transistors par voie (à savoir qu’il y a 2 voies par électrovanne, soit 8 voies pours les 4 électrovannes)

Pour cela, j’ai repris mes cours sur les transistors bipolaires et MOSFET afin de choisir les plus judicieux pour notre système.

# Pour la 3e séance de projet

Fin de la partie IHM du Cahier des charges et validation finale du cahier des charges par toute l’équipe projet.

Validation des schémas de câblage des électrovannes et validation du choix et de la liste finale des composants du projet total.

Début de la programmation de l’IHM sur la base des visuels.

FIN DE COMPTE RENDU – RÉALISÉ LE 26/10/2025 – NEIL AMRANE

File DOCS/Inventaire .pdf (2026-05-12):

Ce tableau correspond à l'inventaire matériel nécessaire pour piloter 4 électrovannes (soit 8 lignes de commande nécessitant chacune une paire de MOSFETs). Les résistances de 33 kΩ servent au pull-up des grilles des MOSFETs P, et celles de 10 kΩ et 4.7 kΩ sont pour les capteurs (Pluie et DHT22).

Composant | Quantité
ESP32 WROOM 32D | 1
Écran TFT (LED) | 1
Batterie 3,7V 20000mAh | 1
Module Booster MT3608 | 1
Module Horloge RTC DS3231 | 1
Capteur DHT22 | 1
Pluviomètre | 1
Électrovannes (3 fils) | 4
MOSFET BSS138 (Canal N) | 8
MOSFET ZXMP6A13FTA (Canal P) | 8
Résistance 33 kΩ | 8
Résistance 10 kΩ | 2
Résistance 4,7 kΩ | 1
Résistance 190 kΩ | 1
Bouton poussoir | 4
Connecteurs / Câbles Dupont | Suffisant

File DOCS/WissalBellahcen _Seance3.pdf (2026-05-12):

Wissal Bellahcen

## Rapport de projet : Programmateur d’arrosage Séance 3

## Introduction

Lors de cette séance, je me suis chargée de l’identification et de l’affectation des GPIO du microcontrôleur ESP32 aux différents éléments du système : écran LED, électrovannes, capteurs et RTC. Cette étape est indispensable pour assurer la faisabilité du câblage et éviter les conflits entre interfaces matérielles (SPI, I²C, entrées analogiques, etc.).
Ma contribution a porté sur l’étude des caractéristiques des broches de l’ESP32, la sélection de celles compatibles avec nos besoins, puis leur affectation définitive dans le projet.

Répartition des broches de l’ESP32

Écran (interface SPI)

- CS → D15
- Reset → D4
- DC → D5
- MOSI (SDI) → D23
- SCK → D18
- MISO (si nécessaire) → D19
- LED (rétroéclairage) → D13 (3,3 V)

Pilotage des électrovannes

- Vanne 1 : Ouverture D16 / Fermeture D17
- Vanne 2 : Ouverture D25 / Fermeture D26
- Vanne 3 : Ouverture D27 / Fermeture D14
- Vanne 4 : Ouverture D32 / Fermeture D33

Wissal Bellahcen

Capteur température / humidité

- Signal → D36 (entrée uniquement)

Horloge RTC (I²C)

- SDA → D22
- SCL → D21

J’ai également vérifié les broches à éviter (GPIO0,2,12,15 + GPIO6→11 liés à la mémoire flash + GPIO1/3 UART) afin de garantir un fonctionnement sans conflit.

Conclusion

Cette séance a permis de finaliser la planification du câblage électronique.
Le travail réalisé facilitera l’intégration et les tests matériels de la prochaine séance, en assurant une organisation claire des connexions entre l’ESP32 et les différents modules du système d’arrosage.

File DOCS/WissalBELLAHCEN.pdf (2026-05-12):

Wissal Bellahcen

## Rapport de projet : Programmateur d’arrosage Séance 1+2

## Introduction

Ce projet vise à réaliser un système d’arrosage automatique pour quatre circuits indépendants, piloté par un ESP32 WIFI. Le système utilise un écran LED et des boutons pour l’interface utilisateur, ainsi que des capteurs de température, hygrométrie et pluviométrie pour adapter l’irrigation aux conditions réelles.

Chaque vanne peut être activée individuellement et fonctionne successivement pour maintenir un débit optimal, avec une durée d’arrosage réglable par circuit. La connectivité WIFI permettra à terme le contrôle à distance et le transfert des données vers un serveur.

### Première séance : Choix des composants et rôle dans le projet

Lors de la première séance, notre groupe a travaillé sur l’élaboration du cahier des charges, définissant les besoins fonctionnels et techniques du système. Ma contribution s’est concentrée sur le choix et la description des composants électroniques principaux :

ESP32 WROOM 32D

L’ESP32 WROOM 32D a été sélectionné comme microcontrôleur central du système. Ce module combine Wi-Fi et Bluetooth et dispose de suffisamment de puissance et de mémoire pour gérer simultanément les électrovannes, les capteurs et l’affichage sur l’écran LED. Dans notre projet, l’ESP32 est responsable de :

- La lecture des capteurs (humidité, température, pluviométrie) pour adapter l’arrosage aux conditions réelles.
- La commande des quatre électrovannes, en assurant que chaque circuit fonctionne de manière autonome mais coordonnée.
- La gestion de la consommation d’énergie, grâce à son processeur ULP qui permet de maintenir certains capteurs actifs en veille.

Cette approche permet de centraliser toutes les fonctions du système sur un seul module puissant et flexible.

Module horloge RTC DS3231

Pour la gestion du temps, nous avons choisi le module RTC DS3231, capable de conserver l’heure même lorsque le système est hors tension grâce à sa pile intégrée. Dans notre projet, la RTC :

- Fournit une référence horaire précise pour planifier les cycles d’arrosage.
- Permet l’affichage de l’heure et de la date sur l’écran LED.
- Facilite l’adaptation de l’arrosage aux besoins spécifiques des différentes zones grâce à la programmation horaire.

En résumé, ces deux composants sont au cœur du fonctionnement du système : l’ESP32 assure le contrôle intelligent et la communication, tandis que la RTC garantit une gestion précise du temps et des cycles d’irrigation.

### Deuxième séance : Programmation des électrovannes

Lors de la deuxième séance, j’ai développé le code Arduino permettant le contrôle de la fermeture et l’ouverture des quatre électrovannes via l’ESP32.

### 3.1 Objectifs du code

- Initialiser les sorties correspondant aux électrovannes
- Définir les fonctions pour ouvrir et fermer chaque vanne
- Fermer toutes les vannes au démarrage pour sécurité
- Tester le fonctionnement via le moniteur série

### 3.2 Fonctionnalités principales

- Ouverture et fermeture d’une vanne spécifique via les fonctions ouvrirVanne(n) et fermerVanne(n)
- Fermeture de toutes les vannes avec fermerLesVannes()
- Boucle principale (loop) testant l’ouverture et la fermeture de la vanne 1 avec un intervalle de 2 secondes

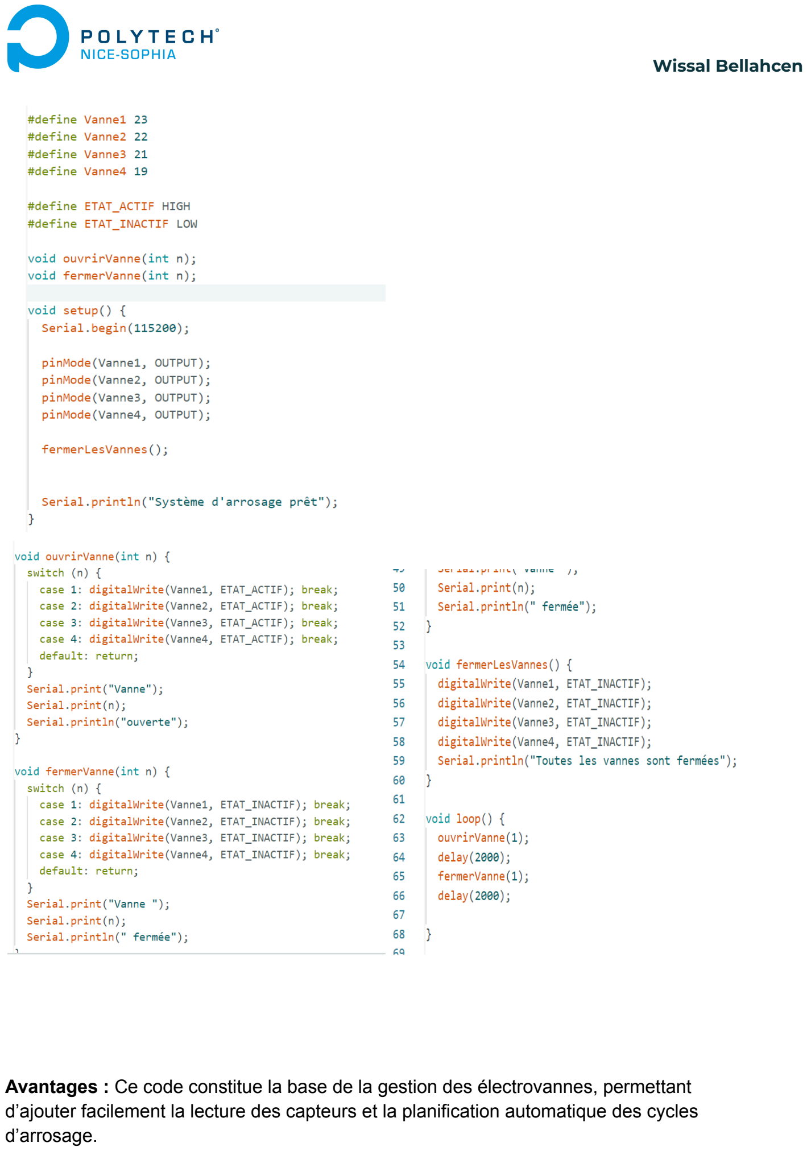
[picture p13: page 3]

Avantages : Ce code constitue la base de la gestion des électrovannes, permettant d’ajouter facilement la lecture des capteurs et la planification automatique des cycles d’arrosage.

## Conclusion

Ces deux premières séances ont permis de définir les composants clés du système et de mettre en place le contrôle logiciel de base des électrovannes. Mon travail a porté sur la documentation technique de l’ESP32 et du module RTC, ainsi que sur le développement du code de pilotage des vannes. Ces bases serviront pour les prochaines étapes : intégration des capteurs et mise en place d’un planning d’arrosage automatisé.

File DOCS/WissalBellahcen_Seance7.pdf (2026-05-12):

# Rapport Séance 7 Migration vers ESP-IDF

## 1 Introduction

Suite aux difficultés rencontrées lors de l’utilisation du coprocesseur ULP avec l’environnement Arduino, une migration vers l’environnement officiel ESP-IDF a été envisagée. Cette décision repose sur le fait que ESP-IDF est le framework natif développé par Espressif, offrant un support complet et maintenu des fonctionnalités avancées de l’ESP32, notamment l’ULP.

## 2 Problématique

Les problèmes identifiés étaient les suivants :
— incompatibilité des versions récentes d’Arduino avec les outils ULP — erreurs de compilation des fichiers assembleur (.S)
— absence de reconnaissance des registres et macros ULP
— dépendance à des bibliothèques non maintenues
Ces limitations rendaient impossible la validation du système basé sur l’ULP.

## 3 Installation de l’environnement

L’installation de ESP-IDF a été réalisée en plusieurs étapes : — installation de Python et des dépendances
— installation du toolchain Xtensa
— configuration des variables d’environnement
— initialisation du projet via idf.py

## 4 Structure du projet

Une architecture modulaire a été adoptée :

project /
main /
main .c
ulp /
ulp_rain .S
CMakeLists . txt

Cette organisation permet une séparation claire entre le programme principal et le programme ULP.

1

## 5 Analyse

L’utilisation de ESP-IDF permet :
— une meilleure gestion de la mémoire RTC
— une compilation native du code ULP
— une compatibilité totale avec les fonctionnalités hardware

## 6 Conclusion

La migration vers ESP-IDF constitue une étape essentielle pour garantir la fiabilité du projet et permettre l’exploitation correcte du coprocesseur ULP.

2

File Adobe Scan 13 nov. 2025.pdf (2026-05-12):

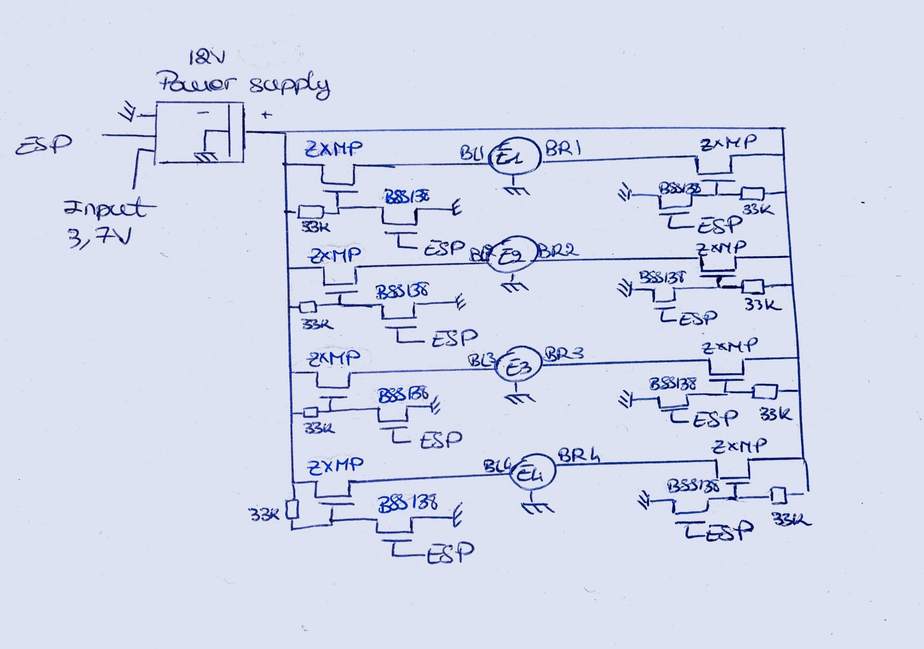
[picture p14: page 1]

~"'X M,.:f> _____ _

-,

~13i e
E&.P

~'r
- --c6s

~131'
~,,_ .----
L6&-P
i~H.-f' 1- 1
~'3 - ~ . "' -C:s;s-p

-2,;XN-P
.,__ ~

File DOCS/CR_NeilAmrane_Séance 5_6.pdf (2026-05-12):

### Neil AMRANE - ELSE 4 FISA - ANNÉE 2025-2026

# Compte rendu Séance 5 & 6

## SYSTÈME D’ARROSAGE AUTOMATIQUE GÉRÉ PAR ESP32

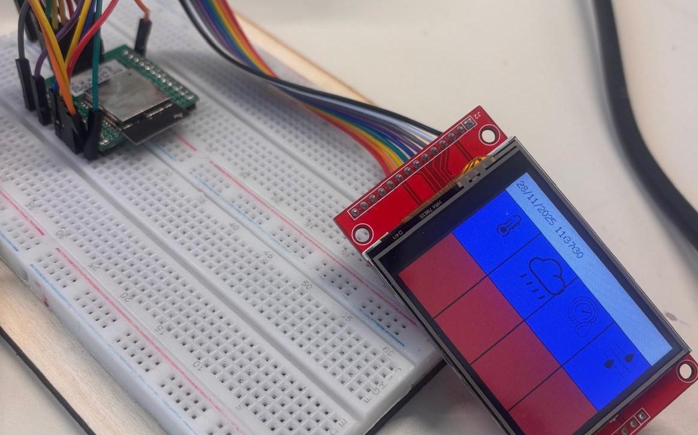
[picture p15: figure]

# Introduction

Le projet “Arrosage Automatique contrôlé par ESP32” est un projet tutoré par Christian Peter dans le cadre du projet d’électronique S7 ELSE 4 FISA. Ce projet est mené en collaboration par Neil Amrane, Salma Elfiache, Wissal Bellahcen et Khady Ndyé Diop.

Cet enseignement a pour but de développer un esprit de collaboration et une dynamique créative tout en favorisant l’autonomie dans la création d’un dispositif fonctionnel. Ce projet permet, en outre, de se familiariser avec l’électronique haut niveau et l’interconnection de différents sous-systèmes électroniques en observant un projet dans sa globalité avec ses tenants et aboutissants.

L’objectif est de créer un système d’arrosage automatique permettant de contrôler 4 voies individuellement en programmant la durée d’arrosage de chaque voie et la fréquence d’arrosage des 4 voies. Ce même système intègre différents capteurs qui permettent de mieux gérer l’irrigation des zones couvertes par les circuits d’arrosage et de préserver la biodiversité en tenant compte des données géologiques et atmosphériques réelles et locales

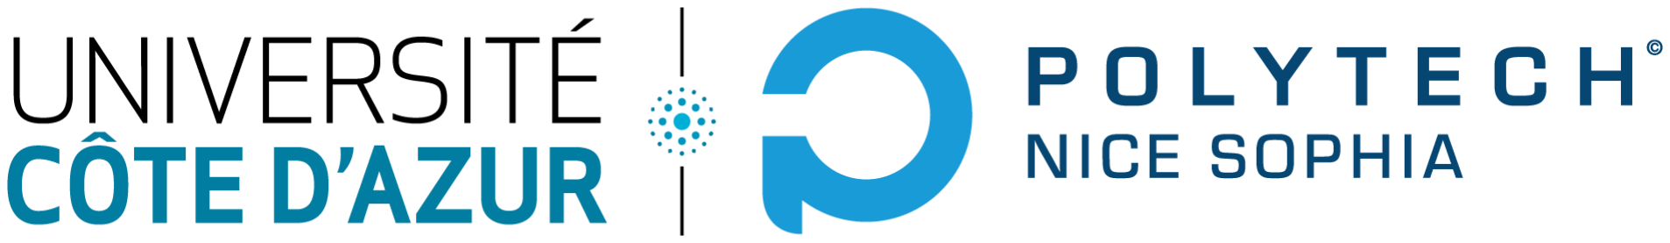
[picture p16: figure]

# Séance 5 & 6 - Clock et Affichage

Lors de la séance 5, j’ai poursuivi la programmation de l’écran d’affichage du système. J’ai débuté la programmation du visuel général à travers les fonctions et procédures de la library “TFT.h” et “e_TFT.h”.

J’ai poursuivi la séance 5 avec le débogage du code du module horloge et j’ai intégré le code dans le programme principal pour afficher l’heure sur l’écran.

J’ai débuté une réflexion autour de la mise à jour en temps réel de l’affichage, afin de ne pas modifier toute l’interface à chaque seconde.

La séance 6 s’inscrit dans la continuité de la cinquième. J’ai commencé à structurer le code sous la forme de sous-fonctions et fonctions auxiliaires.

J’ai poursuivi la programmation de l’écran avec l’ajout d'images PNG (sans fond, donc faisant intervenir la transparence). J’ai du passer par la conversion de mes images PNG en tableau de pixels Hexadécimaux dans un fichier source “images.h”, puis j’ai utilisé la library “PNGDec.h” , ainsi qu’une fonction callback pour récupérer les tableaux d’hexa et les afficher sur l’écran.

Pour la prochaine séance, je poursuivrai la programmation de l’écran, ainsi que la structuration du code, afin de poursuivre avec la récupération des données des capteurs pour les afficher sur l'écran dans les cases correspondantes.

Je suis également en train de réfléchir à la programmation d’un deuxième écran permettant de programmer la durée et la fréquence d’arrosage.

L’algorithme et le code implémentant la logique (le backend), ne font pour l'instant pas partie de ma scope. Je m’occupe pour l’instant que du front.

FIN DE COMPTE RENDU – FAIT À PISE – LE 30/11/2025

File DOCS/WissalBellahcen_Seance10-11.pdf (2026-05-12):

# Rapport Séances 10-11 Réduction du système ULP et stabilisation du comptage

## 1 Contexte

Face aux problèmes persistants de comptage dans l’implémentation ULP complète, une simplification radicale de l’architecture a été adoptée.

## 2 Problème identifié

Les dysfonctionnements observés sont :
— pertes d’impulsions dues au timing ULP
— comptage incorrect dans les transitions rapides — instabilité du signal GPIO34

## 3 Décision technique

Il a été décidé de :
— abandonner la chaîne ULP complexe (bin + .h)
— utiliser une approche directe basée sur les registres RTC — exploiter la bibliothèque soc/rtc_io_reg.h

## 4 Implémentation

#include " so c / r tc_io_ reg . h" #include <Arduino . h>

#def ine PLUVIO_PIN 34

void se tup ( ) {
r t c_g pio_i ni t (GPIO_NUM_34 ) ;
r t c_g pio_ s e t_ di r e c tio n (GPIO_NUM_34, RTC_GPIO_MODE_INPUT_ONLY) ; }

void loo p ( ) {
int s t a t e = REG_READ(RTC_GPIO_IN_REG) ; }

1

## 5 Analyse

Cette approche permet :
— un accès direct au registre GPIO
— une réduction de la complexité logicielle — une meilleure stabilité d’exécution

## 6 Résultat

Le système devient plus stable, mais reste limité en précision sur le comptage des impulsions.

## 7 Conclusion

Cette étape constitue une transition vers une architecture simplifiée permettant de stabiliser le comportement du système.

2

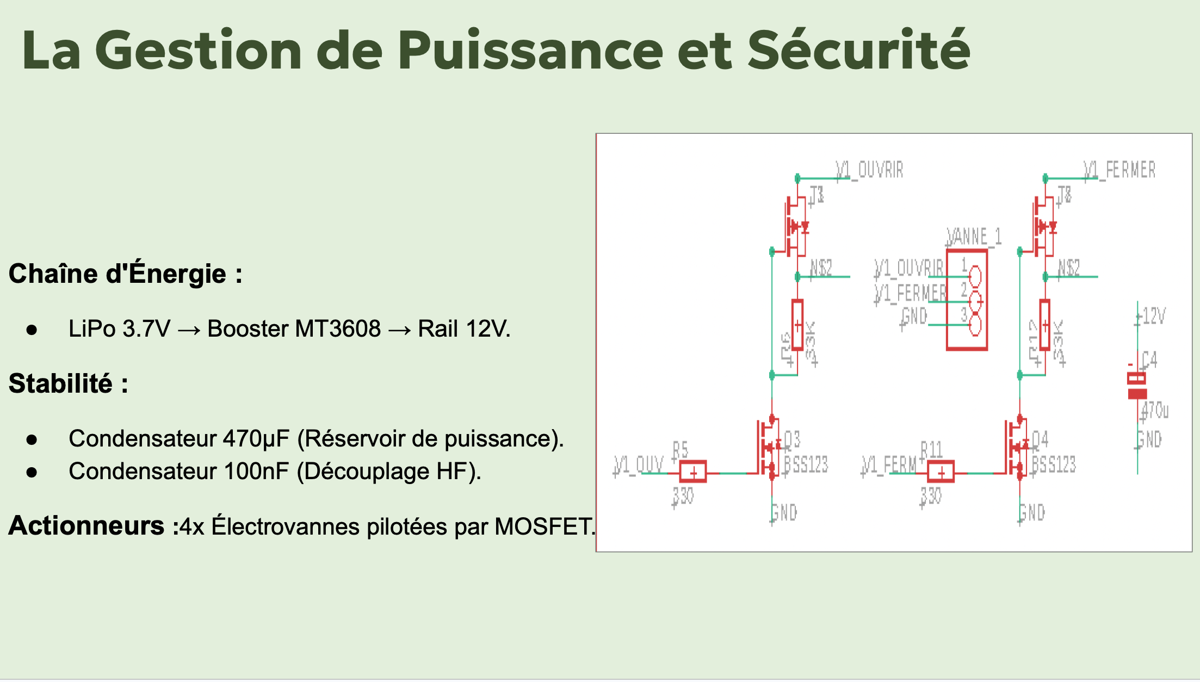
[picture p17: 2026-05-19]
Gestion_energie.png

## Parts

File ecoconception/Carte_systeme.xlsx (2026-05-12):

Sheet: General information
General information
UUID | c781f8ed-e82d-47ec-a414-70245abfc7a3
Name | Carte_systeme
Category
Description
Version | 00.00.005
Last change | 2026-04-29 12:43
Tags
Time
Valid from
Valid until
Description
Geography
Location
Description
Technology
Description
Data quality
Process schema
Data quality entry
Flow schema
Social schema

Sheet: Inputs
Is reference? | Flow | Category | Amount | Unit | Costs/Revenues | Currency | Uncertainty | (G)Mean | Mode | SD | GSD | Minimum | Maximum | Is avoided? | Provider | Data quality entry | Location | Description
 | battery, Li-ion, NMC111, rechargeable | C:Manufacturing/27:Manufacture of electrical equipment/272:Manufacture of batteries and accumulators/2720:Manufacture of batteries and accumulators | 45 | g |  |  |  |  |  |  |  |  | market for battery, Li-ion, NMC111, rechargeable | battery, Li-ion, NMC111, rechargeable | APOS, U
 | brass | C:Manufacturing/24:Manufacture of basic metals/242:Manufacture of basic precious and other non-ferrous metals/2420:Manufacture of basic precious and other non-ferrous metals | 960 | g |  |  |  |  |  |  |  |  | market for brass | brass | APOS, U
 | capacitor, film type, for through-hole mounting | C:Manufacturing/26:Manufacture of computer, electronic and optical products/261:Manufacture of electronic components and boards/2610:Manufacture of electronic components and boards | 0.49 | g |  |  |  |  |  |  |  |  | market for capacitor, film type, for through-hole mounting | capacitor, film type, for through-hole mounting | APOS, U
 | diode, glass-, for through-hole mounting | C:Manufacturing/26:Manufacture of computer, electronic and optical products/261:Manufacture of electronic components and boards/2610:Manufacture of electronic components and boards | 0.064 | g |  |  |  |  |  |  |  |  | market for diode, glass-, for through-hole mounting | diode, glass-, for through-hole mounting | APOS, U
 | electric connector, peripheral component interconnect buss | C:Manufacturing/26:Manufacture of computer, electronic and optical products/261:Manufacture of electronic components and boards/2610:Manufacture of electronic components and boards | 8 | g |  |  |  |  |  |  |  |  | market for electric connector, peripheral component interconnect buss | electric connector, peripheral component interconnect buss | APOS, U
 | electric motor, vehicle | C:Manufacturing/27:Manufacture of electrical equipment/271:Manufacture of electric motors, generators, transformers and electricity distribution and control apparatus/2710:Manufacture of electric motors, generators, transformers and electricity di | 240 | g |  |  |  |  |  |  |  |  | market for electric motor, vehicle | electric motor, vehicle | APOS, U
 | electricity, low voltage | D:Electricity, gas, steam and air conditioning supply/35:Electricity, gas, steam and air conditioning supply/351:Electric power generation, transmission and distribution/3510:Electric power generation, transmission and distribution | 3.18 | kWh |  |  |  |  |  |  |  |  | market for electricity, low voltage | electricity, low voltage | APOS, U
 | inductor, low value multilayer chip | C:Manufacturing/26:Manufacture of computer, electronic and optical products/261:Manufacture of electronic components and boards/2610:Manufacture of electronic components and boards | 0.1 | g |  |  |  |  |  |  |  |  | market for inductor, low value multilayer chip | inductor, low value multilayer chip | APOS, U
 | integrated circuit, logic type | C:Manufacturing/26:Manufacture of computer, electronic and optical products/261:Manufacture of electronic components and boards/2610:Manufacture of electronic components and boards | 6.05 | g |  |  |  |  |  |  |  |  | market for integrated circuit, logic type | integrated circuit, logic type | APOS, U
 | plastic flake, consumer electronics, for recycling | E:Water supply; sewerage, waste management and remediation activities/38:Waste collection, treatment and disposal activities; materials recovery/383:Materials recovery/3830:Materials recovery | 244.6 | g |  |  |  |  |  |  |  |  | market for plastic flake, consumer electronics, for recycling | plastic flake, consumer electronics, for recycling | APOS, U
 | printed wiring board, through-hole mounted, unspecified, Pb containing | C:Manufacturing/26:Manufacture of computer, electronic and optical products/261:Manufacture of electronic components and boards/2610:Manufacture of electronic components and boards | 50 | g |  |  |  |  |  |  |  |  | market for printed wiring board, through-hole mounted, unspecified, Pb containing | printed wiring board, through-hole mounted, unspecified, Pb containing | APOS, U
 | resistor, metal film type, through-hole mounting | C:Manufacturing/26:Manufacture of computer, electronic and optical products/261:Manufacture of electronic components and boards/2610:Manufacture of electronic components and boards | 0.72 | g |  |  |  |  |  |  |  |  | market for resistor, metal film type, through-hole mounting | resistor, metal film type, through-hole mounting | APOS, U
 | transistor, wired, small size, through-hole mounting | C:Manufacturing/26:Manufacture of computer, electronic and optical products/261:Manufacture of electronic components and boards/2610:Manufacture of electronic components and boards | 0.56 | g |  |  |  |  |  |  |  |  | market for transistor, wired, small size, through-hole mounting | transistor, wired, small size, through-hole mounting | APOS, U

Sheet: Outputs
Is reference? | Flow | Category | Amount | Unit | Costs/Revenues | Currency | Uncertainty | (G)Mean | Mode | SD | GSD | Minimum | Maximum | Is avoided? | Provider | Data quality entry | Location | Description
x | Station Arrosage Complète |  | 1.555584 | kg

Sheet: Allocation
Default allocation method | none
Physical & economic allocation
Product | Category | Physical | Economic
Causal allocation
Flow | Category | Direction | Amount | Station Arrosage Complète

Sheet: Parameters
Global input parameters
Name | Value | Uncertainty | (G)Mean | Mode | SD | GSD | Minimum | Maximum | Description
Global calculated parameters
Name | Formula | Description
Input parameters
Name | Value | Uncertainty | (G)Mean | Mode | SD | GSD | Minimum | Maximum | Description
Calculated parameters
Name | Formula | Description

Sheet: Documentation
LCI method
Process type | Unit process
LCI method
Modeling constants
Data source information
Data completeness
Data selection
Data treatment
Sampling procedure
Data collection period
Use advice
Completeness
Sources
Administrative information
Project
Intended application
Data set owner
Data set generator
Data set documentor
Publication
Creation date | 2026-04-22 14:18
Copyright | FALSE
Access and use restrictions

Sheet: Flows
UUID | Name | Description | Category | Version | Last change | Type | CAS | Formula | Location | Reference flow property
779a79ee-7466-4a8b-8440-db906edf68e7 | battery, Li-ion, NMC111, rechargeable | EcoSpold 2 intermediate exchange, ID = 779a79ee-7466-4a8b-8440-db906edf68e7 The product battery, Li-ion, NMC111, rechargeable is a Li-ion battery made with NMC111 cells. A battery is a device that stores chemical energy and converts it to electrical energy. It is made of modules in which cells are packed together and connected through cables. It can be used in the following applications and/or processes: electric vehicles, laptops, energy storage systems | C:Manufacturing/27:Manufacture of electrical equipment/272:Manufacture of batteries and accumulators/2720:Manufacture of batteries and accumulators | 03.11.000 |  | Product flow |  |  |  | Mass
57771ae0-5e8b-47be-bb73-ba59f2bf8cc8 | brass | EcoSpold 2 intermediate exchange, ID = 57771ae0-5e8b-47be-bb73-ba59f2bf8cc8 'brass' is a metal. It is an alloy of 70% copper and 30% zinc as alloying element. They are both transition metals. It is a direct product from metal melting. It is in a form of ingots. It can be used in the following applications and/or processes: variety of products and objects, such as locks, gears, bearings, valves, musical instruments, decorative artifacts, braces, brackets, base plates, etc., decorative purposes primarily because of its resemblance to gold. It is also commonly used to make musical instruments due to its high workability and durability. | C:Manufacturing/24:Manufacture of basic metals/242:Manufacture of basic precious and other non-ferrous metals/2420:Manufacture of basic precious and other non-ferrous metals | 03.11.000 |  | Product flow | 86376-49-0 |  |  | Mass
1edf4d42-6315-49ab-89b8-cd8dd643f43c | capacitor, film type, for through-hole mounting | EcoSpold 2 intermediate exchange, ID = 1edf4d42-6315-49ab-89b8-cd8dd643f43c This is an electric component usually soldered to a printed wiring board (PWB) in electronic circuits. A capacitor stores electrical energy in an electric field between at least two electrical conductors. Film type capacitors use an insulating plastic film as the dielectric. For this product it is assumed that a typical film capacitor has an average weight of 0.7 g. This component is designed for through-hole mounting. | C:Manufacturing/26:Manufacture of computer, electronic and optical products/261:Manufacture of electronic components and boards/2610:Manufacture of electronic components and boards | 03.11.000 |  | Product flow |  |  |  | Mass
0fd2627f-cd91-40c7-b168-8d7847ffb1fc | diode, glass-, for through-hole mounting | EcoSpold 2 intermediate exchange, ID = 0fd2627f-cd91-40c7-b168-8d7847ffb1fc This is an electric component usually soldered to a printed wiring board (PWB) in electronic circuits. A diode conducts electricity in only one direction. Glass diodes consist of a vacuum tube and two electrodes of which one is a heated cathode and the other a plate electrode. For this product it is assumed that a typical through-hole mounting diode in electronic modules has an average weight of 0.596 g. This component is designed for through-hole mounting. | C:Manufacturing/26:Manufacture of computer, electronic and optical products/261:Manufacture of electronic components and boards/2610:Manufacture of electronic components and boards | 03.11.000 |  | Product flow |  |  |  | Mass
97abb774-9c04-4e55-8bc2-94edaff6342d | electric connector, peripheral component interconnect buss | EcoSpold 2 intermediate exchange, ID = 97abb774-9c04-4e55-8bc2-94edaff6342d This product represents an internal connector for computer technology, i.e. the so-called Peripheral Component Interconnect (PCI) bus. It is used to connect devices to the motherboard of a computer. | C:Manufacturing/26:Manufacture of computer, electronic and optical products/261:Manufacture of electronic components and boards/2610:Manufacture of electronic components and boards | 03.11.000 |  | Product flow |  |  |  | Mass
faac50ba-db79-4c84-8c68-9453728f9063 | electric motor, vehicle | EcoSpold 2 intermediate exchange, ID = faac50ba-db79-4c84-8c68-9453728f9063 This product represents 1 kg of a small electric motor used in electric vehicles such as electric bicycles. | C:Manufacturing/27:Manufacture of electrical equipment/271:Manufacture of electric motors, generators, transformers and electricity distribution and control apparatus/2710:Manufacture of electric motors, generators, transformers and electricity di | 03.11.000 |  | Product flow |  |  |  | Mass
d69294d7-8d64-4915-a896-9996a014c410 | electricity, low voltage | EcoSpold 2 intermediate exchange, ID = d69294d7-8d64-4915-a896-9996a014c410 This product represents electrical energy measured in kWh. If electricity is taken from a market for electricity, the transmission infrastructure, country-specific losses and transformation losses (for markets for medium and low voltage) are included. Covers voltages below 1 kV. | D:Electricity, gas, steam and air conditioning supply/35:Electricity, gas, steam and air conditioning supply/351:Electric power generation, transmission and distribution/3510:Electric power generation, transmission and distribution | 03.11.000 |  | Product flow |  |  |  | Energy
736906f7-164e-4155-9fb4-894177303917 | inductor, low value multilayer chip | EcoSpold 2 intermediate exchange, ID = 736906f7-164e-4155-9fb4-894177303917 This is an electric component usually soldered to a printed wiring board (PWB) in electronic circuits. An inductor stores energy in a magnetic field when an electric current flows through it. For this product it is assumed that a typical low value multilayer chip type inductor electronic module has an average weight of 2.1 milligrams. | C:Manufacturing/26:Manufacture of computer, electronic and optical products/261:Manufacture of electronic components and boards/2610:Manufacture of electronic components and boards | 03.11.000 |  | Product flow |  |  |  | Mass
ad2a5d44-4e6d-430d-873b-0068ea24b9d5 | integrated circuit, logic type | EcoSpold 2 intermediate exchange, ID = ad2a5d44-4e6d-430d-873b-0068ea24b9d5 This is an electric component usually soldered to a printed wiring board (PWB) in electronic circuits. Integrated circuits are electronic circuits etched in a semiconducting material (usually silicon) by photolithography and enclosed in a package to protect the circuit. Logic type circuits perform specified logical operations on incoming data. | C:Manufacturing/26:Manufacture of computer, electronic and optical products/261:Manufacture of electronic components and boards/2610:Manufacture of electronic components and boards | 03.11.000 |  | Product flow |  |  |  | Mass
a9b2fe27-bc40-4a22-a2c8-e320425c0086 | plastic flake, consumer electronics, for recycling | EcoSpold 2 intermediate exchange, ID = a9b2fe27-bc40-4a22-a2c8-e320425c0086 'plastic flake, consumer electronics, for recycling' is a solid waste under the category of industrial wastes. It is primarily generated in grinding and shredding of consumer electronics. 'plastic flake, consumer electronics, for recycling' contain the following fractions: 100% plastic flake. By the database default (and per unit of reference product),'plastic flake, consumer electronics, for recycling' has 0% water on wet mass basis (100% dry matter) and it has no Carbon content. It has a lower heating value of 34.78 MJ/kg . This kind of by-product (recyclable or waste) is generated from ordinary transforming activities, and as such can be considered for modelling waste outputs of comparable composition. In the ecoinvent database, this by-product is used in the following processes: plastic granulate production, unspecified, recycled, formal sector; plastic granulate production, unspecified, recycled, informal sector. This by-product can be modelled on two levels: treatment activity and market activity. The former one refers to the specific technology treating the by-product while the latter level represents a mix of treatments. Users are encouraged to inspect the modelling assumptions of the treatment activities and when selecting the market to additionally inspect the treatment mix. Collection and transportation of this by-product is accounted in the respective market activity, users are advised t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 | E:Water supply; sewerage, waste management and remediation activities/38:Waste collection, treatment and disposal activities; materials recovery/383:Materials recovery/3830:Materials recovery | 03.11.000 |  | Product flow |  |  |  | Mass
40521328-bdae-4fc3-9034-cd8bea5c7fa2 | printed wiring board, through-hole mounted, unspecified, Pb containing | EcoSpold 2 intermediate exchange, ID = 40521328-bdae-4fc3-9034-cd8bea5c7fa2 This product represents 1 kg of a mounted printed wiring board for unspecified applications. The product is a mounted printed wiring board, meaning the electronic components such as capacitors, resistors etc. have been soldered to the board. The solder and surface used for mounting the components is lead containing. | C:Manufacturing/26:Manufacture of computer, electronic and optical products/261:Manufacture of electronic components and boards/2610:Manufacture of electronic components and boards | 03.11.000 |  | Product flow |  |  |  | Mass
92d9032c-7554-43a7-87b7-59ced4c2516a | resistor, metal film type, through-hole mounting | EcoSpold 2 intermediate exchange, ID = 92d9032c-7554-43a7-87b7-59ced4c2516a This is an electric component usually soldered to a printed wiring board (PWB) in electronic circuits. Resistors are used to reduce electric current and the voltage in an electric circuit. For this product it is assumed that a typical metal film type resistor electronic module has an average weight of 0.48 g. Metal film type resistors are manufactured by depositing a metal film on an insulating substrate. This component is designed for through-hole mounting. | C:Manufacturing/26:Manufacture of computer, electronic and optical products/261:Manufacture of electronic components and boards/2610:Manufacture of electronic components and boards | 03.11.000 |  | Product flow |  |  |  | Mass
e9f8091a-8a88-41be-9e54-08f5d878a998 | Station Arrosage Complète |  |  | 00.00.000 | 2026-04-22 14:15 | Product flow |  |  |  | Mass
233843d2-7fda-443f-8735-547f06711c6d | transistor, wired, small size, through-hole mounting | EcoSpold 2 intermediate exchange, ID = 233843d2-7fda-443f-8735-547f06711c6d This is an electric component usually soldered to a printed wiring board (PWB) in electronic circuits. Transistors are made of semiconductor material and are used to switch or amplify electric signals. For this product it is assumed that a wired, small-size transistor in electronic modules has an average weight of 0.818 g. This component is designed for through-hole mounting. | C:Manufacturing/26:Manufacture of computer, electronic and optical products/261:Manufacture of electronic components and boards/2610:Manufacture of electronic components and boards | 03.11.000 |  | Product flow |  |  |  | Mass

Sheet: Flow properties
UUID | Name | Description | Category | Unit group | Type | Version | Last change
f6811440-ee37-11de-8a39-0800200c9a66 | Energy |  | Technical flow properties | Units of energy | Physical | 02.08.000
93a60a56-a3c8-11da-a746-0800200b9a66 | Mass |  | Technical flow properties | Units of mass | Physical | 02.08.000

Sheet: Unit groups
UUID | Name | Category | Description | Reference unit | Default flow property | Version | Last change
93a60a57-a3c8-11da-a746-0800200c9a66 | Units of energy | Technical unit groups |  | MJ | Energy | 02.08.000
93a60a57-a4c8-11da-a746-0800200c9a66 | Units of mass | Technical unit groups |  | kg | Mass | 02.08.000

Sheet: Units
UUID | Name | Unit group | Description | Synonyms | Conversion factor
55244053-94ba-404e-9172-cb279d905e00 | btu | Units of energy | British thermal unit (International Table) |  | 0.0010551
01e58eb9-0aba-4c76-ba0c-03f6f3be1353 | GJ | Units of energy | Gigajoule |  | 1000
469d61f1-3bc4-4841-8adf-873825c1bc11 | J | Units of energy | Joule |  | 1e-06
010f811e-3cc2-4b14-a901-337da9b3e49c | kcal | Units of energy | Kilocalorie (International Table) |  | 0.004184
f4119718-2d50-47fe-9154-cab6fd2d30eb | kJ | Units of energy | Kilojoule |  | 0.001
86ad2244-1f0e-4912-af53-7865283103e4 | kWh | Units of energy | Kilowatt times hour |  | 3.6
52765a6c-3896-43c2-b2f4-c679acf13efe | MJ | Units of energy | Megajoule |  | 1
92e3bd49-8ed5-4885-9db6-fc88c7afcfcb | MWh | Units of energy | Megawatt times hour |  | 3600
ff1a332f-967c-4084-8b01-8d3ca81b3121 | PJ | Units of energy | Petajoule |  | 1000000000
787f2ac9-7bcd-4a91-9fab-55bfe414138f | TCE | Units of energy | Tonne coal equivalent |  | 29307.6
57c492e7-d94b-4fcc-98df-cdc4163b754c | TJ | Units of energy | Terajoule |  | 1000000
425aff51-b7e5-4561-aa5a-562ec103a79e | TOE | Units of energy | Tonne oil equivalent |  | 41868
fc3604f7-aa93-4aa3-8ae9-8f822874da5f | Wh | Units of energy | Watt times hour |  | 0.0036
218bf752-ec01-43a9-b87c-0e733374fffd | cg | Units of mass | Centigram |  | 1e-05
ae5cced9-f9f1-4719-bd37-837b36013d96 | ct | Units of mass | Matric carat | carat | 0.0002
2a0b9356-a2dd-444f-991e-ce66cd174c9e | cwt | Units of mass | Short hundredweight |  | 45.359237
90d59045-3565-4c5a-bb27-ebc365aacbd0 | dag | Units of mass | Decagram |  | 0.01
2ac22d0d-9e02-4459-9402-923490e4e1b4 | dg | Units of mass | Decigram |  | 0.0001
56f42b51-bb05-4dcd-a069-0693f167304c | dr (Av) | Units of mass | Dram (Avoirdupois) |  | 0.001771845195
a3350a8a-5cb0-440d-9752-8afe8c08c455 | dwt | Units of mass | Pennyweight |  | 0.001555174
e1317ffc-7f83-4a85-bc65-4fb229a25cf8 | g | Units of mass | Gram |  | 0.001
78af80e7-ede4-4a65-b04d-97d9ce4f39d3 | grain | Units of mass | Grain | gr | 6.479891e-05
86dfd16d-d1d8-4b71-88af-0e1126425c77 | hg | Units of mass | Hectogram |  | 0.1
20aadc24-a391-41cf-b340-3e4529f44bde | kg | Units of mass | Kilogram |  | 1
95dd50e9-c184-4412-9afc-9764b1ffcf8f | kg SWU | Units of mass | Kilogram (Separative Work Unit) |  | 1
e720c842-19f5-4a38-8573-78dd13719f5b | kt | Units of mass | Kilotonne |  | 1000000
0300ec69-ce1a-45f0-bcf0-7b33845dc53e | lb av | Units of mass | British pound (Avoirdupois) | lb | 0.45359237
e5ccc940-eb40-41f9-847e-5ee691ba8c2f | long tn | Units of mass | Long ton | tn.lg | 1016.047
d022bf34-1162-4579-90ab-dcca9620ce54 | Mg | Units of mass | Megagram |  | 1000
b872a063-0500-42b7-9e5d-441642d84417 | mg | Units of mass | Milligram |  | 1e-06
9dd23b40-4394-4f9a-9572-5f2ee9643864 | Mt | Units of mass | Megatonne | Mtn | 1000000000
63214902-17d4-41a0-be10-d1cad375c32e | ng | Units of mass | Nanogram |  | 1e-12
fa44e424-f37b-419d-8475-723429d63c08 | oz av | Units of mass | Ounce (Avoirdupois) | oz | 0.02834952313
2457aee5-c7ee-4416-a65a-5be4ff2b2976 | oz t | Units of mass | Ounce (Troy) |  | 0.0311034768
68c83ad3-bc5b-414a-81f7-5b47af2c8a23 | pg | Units of mass | Picogram |  | 1e-15
d4922696-9c95-4b5d-a876-425e98276978 | sh tn | Units of mass | Short ton | tn.sh | 907.18
83192ffa-5990-490b-a23a-b45ca072db6f | t | Units of mass | Tonne | ton | 1000
d01259b2-24c2-46af-a7fe-36dd025ead15 | ug | Units of mass | Microgram | µg | 1e-09

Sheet: Currencies
UUID | Name | Category | Description | Last change | Version | Code | Is reference? | Conversion factor

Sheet: Locations
UUID | Code | Name | Category | Description | Latitude | Longitude | Last change | Version

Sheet: Actors
UUID | Name | Description | Category | Version | Last change | Address | City | Zip code | Country | E-Mail | Telefax | Telephone | Website

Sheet: Sources
UUID | Name | Description | Category | Version | Last change | URL | Text reference | Year

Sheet: Providers
UUID | Name | Category | Location
9c3c0106-a9ee-3893-a2d8-bc1b2c9d7c5b | market for battery, Li-ion, NMC111, rechargeable | battery, Li-ion, NMC111, rechargeable | APOS, U | C:Manufacturing/27:Manufacture of electrical equipment/272:Manufacture of batteries and accumulators/2720:Manufacture of batteries and accumulators | Global
49c66086-d19f-3285-a9ef-216dfa614902 | market for brass | brass | APOS, U | C:Manufacturing/24:Manufacture of basic metals/242:Manufacture of basic precious and other non-ferrous metals/2420:Manufacture of basic precious and other non-ferrous metals | Switzerland
7092d7e7-d95b-3ee8-9536-f2cc56da8d85 | market for capacitor, film type, for through-hole mounting | capacitor, film type, for through-hole mounting | APOS, U | C:Manufacturing/26:Manufacture of computer, electronic and optical products/261:Manufacture of electronic components and boards/2610:Manufacture of electronic components and boards | Global
42516f55-0464-3b20-8e3d-cd4ceb36d6aa | market for diode, glass-, for through-hole mounting | diode, glass-, for through-hole mounting | APOS, U | C:Manufacturing/26:Manufacture of computer, electronic and optical products/261:Manufacture of electronic components and boards/2610:Manufacture of electronic components and boards | Global
10d8d76d-5e26-3920-8cc1-97979cfc1d0f | market for electric connector, peripheral component interconnect buss | electric connector, peripheral component interconnect buss | APOS, U | C:Manufacturing/26:Manufacture of computer, electronic and optical products/261:Manufacture of electronic components and boards/2610:Manufacture of electronic components and boards | Global
5d78d712-4cc9-3ed2-9f3a-595738edd598 | market for electric motor, vehicle | electric motor, vehicle | APOS, U | C:Manufacturing/27:Manufacture of electrical equipment/271:Manufacture of electric motors, generators, transformers and electricity distribution and control apparatus/2710:Manufacture of electric motors, generators, transformers and electricity di | Global
b5146f44-d27e-35b4-91d1-c886de607a8c | market for electricity, low voltage | electricity, low voltage | APOS, U | D:Electricity, gas, steam and air conditioning supply/35:Electricity, gas, steam and air conditioning supply/351:Electric power generation, transmission and distribution/3510:Electric power generation, transmission and distribution | France
16d8d9e6-fcc6-3511-ab20-9097344f84b1 | market for inductor, low value multilayer chip | inductor, low value multilayer chip | APOS, U | C:Manufacturing/26:Manufacture of computer, electronic and optical products/261:Manufacture of electronic components and boards/2610:Manufacture of electronic components and boards | Global
cd37ca06-5bd4-3ab8-9c53-60df31c15c1b | market for integrated circuit, logic type | integrated circuit, logic type | APOS, U | C:Manufacturing/26:Manufacture of computer, electronic and optical products/261:Manufacture of electronic components and boards/2610:Manufacture of electronic components and boards | Global
03fd3f5c-52a4-3237-a455-b4223a60e3d5 | market for plastic flake, consumer electronics, for recycling | plastic flake, consumer electronics, for recycling | APOS, U | E:Water supply; sewerage, waste management and remediation activities/38:Waste collection, treatment and disposal activities; materials recovery/383:Materials recovery/3830:Materials recovery | Global
b691155e-6241-361d-92af-a0a03646bbaa | market for printed wiring board, through-hole mounted, unspecified, Pb containing | printed wiring board, through-hole mounted, unspecified, Pb containing | APOS, U | C:Manufacturing/26:Manufacture of computer, electronic and optical products/261:Manufacture of electronic components and boards/2610:Manufacture of electronic components and boards | Global
1d735fce-e9cd-3cac-93cd-2b2e3c0d05bf | market for resistor, metal film type, through-hole mounting | resistor, metal film type, through-hole mounting | APOS, U | C:Manufacturing/26:Manufacture of computer, electronic and optical products/261:Manufacture of electronic components and boards/2610:Manufacture of electronic components and boards | Global
63af12d8-9f88-3965-9894-51887ca9b82d | market for transistor, wired, small size, through-hole mounting | transistor, wired, small size, through-hole mounting | APOS, U | C:Manufacturing/26:Manufacture of computer, electronic and optical products/261:Manufacture of electronic components and boards/2610:Manufacture of electronic components and boards | Global

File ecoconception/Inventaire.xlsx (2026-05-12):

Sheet: inventaire
Bloc logique | Composant | Référence / Valeur | Quantité | Empreinte | ecoinvent
Microcontrôleur | Module ESP32 | ESP-WROOM-32 | 1 | Module PCB | electronic component, integrated circuit, unspecified
Microcontrôleur | Résistance pull-up EN | 10 kΩ | 1 | 805 | resistor, surface mount
Microcontrôleur | Condensateur anti-rebond | 100 nF | 1 | 805 | capacitor, ceramic, surface mount
Microcontrôleur | Condensateur filtrage 3.3V | 10 µF | 1 | 1206 | capacitor, electrolytic, surface mount
Microcontrôleur | Condensateur filtrage 3.3V | 100 nF | 2 | 805 | capacitor, ceramic, surface mount
Alimentation boost | IC MT3608 | MT3608 | 1 | SOT23-6 | integrated circuit, DC-DC converter
Alimentation boost | Inductance | 22 µH | 1 |  | inductor, surface mount
Alimentation boost | Diode Schottky | SS34 | 1 | SMA | diode, Schottky, surface mount
Alimentation boost | Condensateur entrée/sortie | 22 µF | 2 | 1206 | capacitor, ceramic, surface mount
Alimentation boost | Résistance pont diviseur | à calculer | 2 | 805 | resistor, surface mount
Puissance (1 vanne) | MOSFET N-BSS123 | BSS123 | 2 | SOT-23 | transistor, MOSFET, small signal
Puissance (1 vanne) | MOSFET P-AO3401 | AO3401 | 2 | SOT-23 | transistor, MOSFET, power
Puissance (1 vanne) | Résistance pull-up P-MOS | 10 kΩ | 2 | 805 | resistor, surface mount
Puissance (1 vanne) | Résistance grille N-MOS | 330 Ω | 2 | 805 | resistor, surface mount
Puissance (1 vanne) | Bornier 3 broches | Connecteur vanne | 1 |  | connector, unspecified
Multiplicateur x4 vannes
RTC | Module DS3231 | DS3231 | 1 | SOIC-16 | integrated circuit, real-time clock
RTC | Support pile bouton | CR2032 holder | 1 |  | battery holder, surface mount
RTC | Condensateur filtrage | 100 nF | 1 | 805 | capacitor, ceramic
RTC | Résistance pull-up I2C | 4.7 kΩ | 2 | 805 | resistor, surface mount
Capteurs | DHT22 | DHT22 | 1 |  | humidity/temperature sensor, electronic
Capteurs | Résistance pull-up DHT22 | 10 kΩ | 1 | 805 | resistor
Capteurs | Résistance série | 100 Ω (ou 330) | 1 | 805 | resistor
Capteurs | Bornier pluviomètre | 2 broches | 1 |  | connector
Connectique | Header 8 broches (écran) |  | 1 |  | connector, pin header
Connectique | Header 6 broches (FTDI) |  | 1 |  | connector, pin header
Connectique | Header 5 broches (batterie) |  | 1 |  | connector, pin header
Connectique | Header I2C (5 broches) |  | 1 |  | connector, pin header

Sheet: Correspondance
Composant original | Code ecoinvent proposé | Remarque
Module ESP32 |  | À chercher : integrated circuit, microcontroller
Résistance 10kΩ | resistor | surface mount | 10kΩ
Condensateur 100nF | capacitor | ceramic | 100nF
MOSFET BSS123 | transistor | MOSFET | small signal | SOT-23
MT3608 | integrated circuit | DC-DC converter
Diode SS34 | diode | Schottky

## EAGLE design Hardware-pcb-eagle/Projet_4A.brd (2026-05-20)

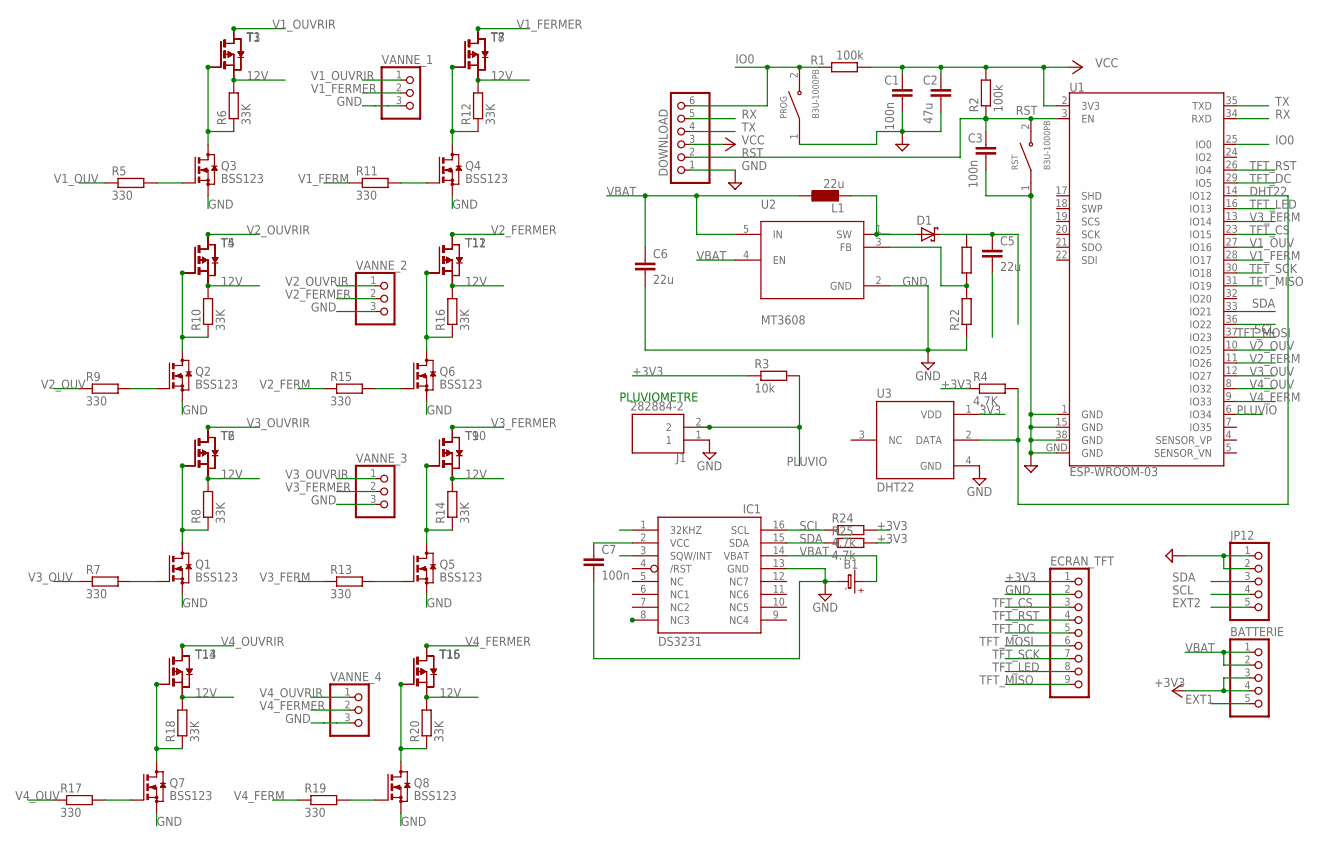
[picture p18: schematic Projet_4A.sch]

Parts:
B1: BATTERYCR2032_BAT-HLD-001; CR2032_SMT_BAT-HLD-001
BATTERIE: PINHD-1X5S; 1X05S
C1, C3, C7: 100n; C0805
C2: 47u; C0805
C5, C6: 22u; C0805
D1: SCHOTTKY-DIODEAG; AG
DOWNLOAD: PINHD-1X6S; 1X06S
ECRAN_TFT: PINHD-1X9; 1X09
IC1: DS3231/SO; SO16W
J1: 282884-2; TE_282884-2
JP12: PINHD-1X5S; 1X05S
L1: 22u; 0204/7
PROG: B3U-1000PB; SW_B3U-1000PB
Q1, Q2, Q3, Q4, Q5, Q6, Q7, Q8: BSS123; SOT23
R1, R2: 100k; R1206
R3: 10k; R0805
R4: 4,7K; 0207/10
R5, R7, R9, R11, R13, R15, R17, R19: 330; 0207/10
R6, R8, R10, R12, R14, R16, R18, R20: 33K; 0207/10
R22: R-EU_0204/2V; 0204V
R24: 4,7k; 0204V
R25: 4.7k; 0204V
RST: B3U-1000PB; SW_B3U-1000PB
T1, T2, T3, T4, T5, T6, T7, T8, T9, T10, T11, T12, T13, T14, T15, T16: PMOSSOT23; SOT-23
U1: ESP-WROOM-03
U2: MT3608; SOT95P280X145-6N
U3: DHT22; XDCR_DHT22
VANNE_1, VANNE_2, VANNE_3, VANNE_4: PINHD-1X3; 1X03

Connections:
3V3: U3.1 (VDD)
12V: C5.1, D1.C, R6.2, R8.2, R10.2, R12.2, R14.2, R16.2, R18.2, R20.2, T1.2 (S), T2.2 (S), T3.2 (S), T4.2 (S), T5.2 (S), T6.2 (S), T7.2 (S), T8.2 (S), T9.2 (S), T10.2 (S), T11.2 (S), T12.2 (S), T13.2 (S), T14.2 (S), T15.2 (S), T16.2 (S)
+3V3: BATTERIE.3, BATTERIE.4, C7.1, ECRAN_TFT.1, IC1.2 (VCC), R3.1, R4.1, R24.2, R25.2
+12V: Q3.3 (D), R6.1, T1.3 (G), T3.3 (G)
+12V1: Q2.3 (D), R10.1, T4.3 (G), T5.3 (G)
+12V2: Q1.3 (D), R8.1, T2.3 (G), T6.3 (G)
+12V3: Q4.3 (D), R12.1, T7.3 (G), T8.3 (G)
+12V4: Q5.3 (D), R14.1, T9.3 (G), T10.3 (G)
+12V5: Q6.3 (D), R16.1, T11.3 (G), T12.3 (G)
+12V6: Q7.3 (D), R18.1, T13.3 (G), T14.3 (G)
+12V7: Q8.3 (D), R20.1, T15.3 (G), T16.3 (G)
DHT22: R4.2, U1.14 (IO12), U3.2 (DATA)
EXT1: BATTERIE.5
EXT2: JP12.5
GND: B1.-, C1.2, C2.2, C3.2, C6.2, C7.2, DOWNLOAD.1, ECRAN_TFT.2, IC1.13 (GND), J1.1, JP12.1, JP12.2, PROG.1, Q1.2 (S), Q2.2 (S), Q3.2 (S), Q4.2 (S), Q5.2 (S), Q6.2 (S), Q7.2 (S), Q8.2 (S), R22.1, RST.1, U1.1 (GND), U1.15 (GND), U1.38 (GND), U1.GND, U2.2 (GND), U3.4 (GND), VANNE_1.3, VANNE_2.3, VANNE_3.3, VANNE_4.3
GND1: C5.2
IO0: DOWNLOAD.6, PROG.2, R1.2, U1.25 (IO0)
unnamed: Q3.1 (G), R5.2
unnamed: Q2.1 (G), R9.2
unnamed: Q1.1 (G), R7.2
unnamed: Q4.1 (G), R11.2
unnamed: Q5.1 (G), R13.2
unnamed: Q6.1 (G), R15.2
unnamed: Q7.1 (G), R17.2
unnamed: Q8.1 (G), R19.2
unnamed: D1.A, L1.2, U2.1 (SW)
unnamed: R22.2, U2.3 (FB)
PLUVIO: J1.2, R3.2, U1.6 (IO34)
RST: C3.1, DOWNLOAD.2, R2.1, RST.2, U1.3 (EN)
RX: DOWNLOAD.5, U1.34 (RXD)
SCL: IC1.16 (SCL), JP12.4, R24.1, U1.36 (IO22)
SDA: IC1.15 (SDA), JP12.3, R25.1, U1.33 (IO21)
TFT_CS: ECRAN_TFT.3, U1.23 (IO15)
TFT_DC: ECRAN_TFT.5, U1.29 (IO5)
TFT_LED: ECRAN_TFT.8, U1.16 (IO13)
TFT_MISO: ECRAN_TFT.9, U1.31 (IO19)
TFT_MOSI: ECRAN_TFT.6, U1.37 (IO23)
TFT_RST: ECRAN_TFT.4, U1.26 (IO4)
TFT_SCK: ECRAN_TFT.7, U1.30 (IO18)
TX: DOWNLOAD.4, U1.35 (TXD)
V1_FERM: R11.1, U1.28 (IO17)
V1_FERMER: T7.1 (D), T8.1 (D), VANNE_1.2
V1_OUV: R5.1, U1.27 (IO16)
V1_OUVRIR: T1.1 (D), T3.1 (D), VANNE_1.1
V2_FERM: R15.1, U1.11 (IO26)
V2_FERMER: T11.1 (D), T12.1 (D), VANNE_2.2
V2_OUV: R9.1, U1.10 (IO25)
V2_OUVRIR: T4.1 (D), T5.1 (D), VANNE_2.1
V3_FERM: R13.1, U1.13 (IO14)
V3_FERMER: T9.1 (D), T10.1 (D), VANNE_3.2
V3_OUV: R7.1, U1.12 (IO27)
V3_OUVRIR: T2.1 (D), T6.1 (D), VANNE_3.1
V4_FERM: R19.1, U1.9 (IO33)
V4_FERMER: T15.1 (D), T16.1 (D), VANNE_4.2
V4_OUV: R17.1, U1.8 (IO32)
V4_OUVRIR: T13.1 (D), T14.1 (D), VANNE_4.1
VBAT: B1.+$1 (+), B1.+$2 (+), BATTERIE.1, BATTERIE.2, C6.1, IC1.14 (VBAT), L1.1, U2.4 (EN), U2.5 (IN)
VCC: C1.1, C2.1, DOWNLOAD.3, R1.1, R2.2, U1.2 (3V3)

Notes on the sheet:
PLUVIOMETRE

Board: 2 copper layers, 71 parts (0 on the bottom side), 54 nets, no tracks yet.

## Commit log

2025-10-26 Add technical documentation for irrigation system sensors
2025-11-09 Add documentation for DHT11 sensor implementation
    Document the implementation and testing of the DHT11 sensor for measuring temperature and humidity in an automatic irrigation system, including installation, wiring, test code, and observations.
2025-11-16 Seance 4
    Document the implementation and validation of the DHT22 sensor and the Lexca001 rain gauge integration.
2025-11-22 Add documentation for battery management and ULP coprocessor
    Document the study of battery management and ULP coprocessor integration for ESP32, including collaborative work on rain gauge sensor integration and energy-saving strategies.
2025-11-22 Enhance documentation on battery management and ULP
    Added details about ULP coprocessor functionality and battery management strategies.
2025-11-22 Rename DOCS/Rapport de projet _ S3.pdf to WissalBellahcen _ Seance3.pdf
2025-11-30 Add documentation for ULP rain gauge project
    Document the process of using the ULP coprocessor on ESP32 to count rain gauge pulses, including challenges faced and solutions implemented.
2025-11-30 Seances 5 et 6
    This document details the implementation and testing of the Lexca001 rain gauge and soil moisture sensor for an automatic irrigation system. It includes wiring diagrams, code examples, and calibratio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
2026-01-04 Add documentation for electronic schematic design
    This document details the electronic schematic design process using Eagle, focusing on power management and component integration for an ESP32-based system.
2026-01-11 Mise a jour de tout le projet
    A valider sur HardWare mais normalement ca marche
2026-02-15 Add documentation for electronic schematic design
    Document the design and implementation of the electronic schematic, including power management, sensor interfaces, and user interface.
2026-03-15 Add documentation for ESP32 firmware architecture
    Document the architecture and functionalities of the firmware for the ESP32 microcontroller, including the design approach, optimization techniques, and future development plans.
2026-04-28 Suppression des fichiers obsolètes (Code_principal.ino à ulptool.h)
2026-05-12 Suppression du dossier data de la branche main
2026-05-20 Ajout du dossier Hardware-pcb-eagle (schémas PCB Eagle)
    [Projet_4A.brd, Projet_4A.sch, Projet_4A_Arrosage_Automatique1.brd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]
